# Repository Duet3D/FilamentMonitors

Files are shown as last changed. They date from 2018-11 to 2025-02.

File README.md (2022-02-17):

# Duet3D Filament monitor hardware source files:

2 Variations:

## Magnetic Filament Monitor

https://www.duet3d.com/magneticfilamentmonitor

Documentation:
https://docs.duet3d.com/Duet3D_hardware/Accessories/Rotating_Magnet_Filament_Monitor

## Laser Filament Monitor
_This is no longer produced_

Documentation for reference:
https://docs.duet3d.com/Duet3D_hardware/Accessories/Laser_Filament_Monitor

## Support requests

Please use the [forum](https://forum.duet3d.com) for support requests.

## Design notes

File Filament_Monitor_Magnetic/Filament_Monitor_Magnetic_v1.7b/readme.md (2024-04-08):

Note the PCB version 1.17b was renamed to version 3.0 so the entire MFM assembly (enclosure, hobbed magnet assembly and PCB) is named version 3.

The PCB itself is unchabed other than the sikscreen labelling.

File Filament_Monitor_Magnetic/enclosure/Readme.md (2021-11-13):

Note: The enclosure is not specifically designed for FDM printing - it is possible to print it on an FDM machine but layer height tweaking/sanding will be required to acheive the correct magnet to sensor offset.

If you have issues downloading the individual stls there is a zip containing all three.

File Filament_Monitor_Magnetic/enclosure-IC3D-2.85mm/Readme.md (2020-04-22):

This enclosure design was kindly provided by IC3D https://ic3dprinters.com/

They made the following changes:

* Thickened the overall body by 3mm
* Switched from using the plastic alignment ‘bumps’ to using 3mm stainless alignment pins
* Adjusted the position of the alignment pins
* Adjusted the filament through hole to 3mm dia.
* Printed in PCPBT

Please note it is still under development. Any questions please use the Duet3D forum: https://forum.duet3d.com/category/17/filament-monitor

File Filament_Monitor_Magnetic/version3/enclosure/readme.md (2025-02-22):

This is the FDM 3d printable version of the housing. Use this if you want to print your own housing.

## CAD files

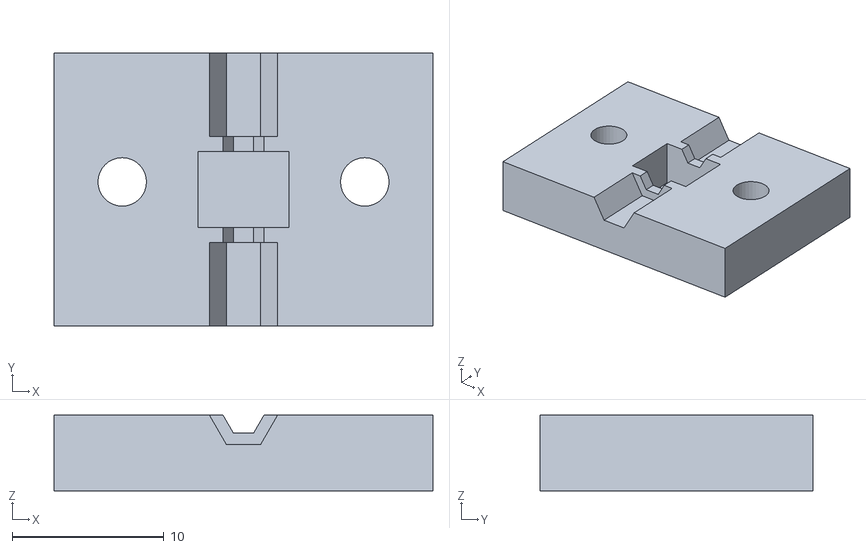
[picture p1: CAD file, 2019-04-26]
Filament_Monitor_Laser/Filament_Monitor_Laser_v2.0/LaserFilamentSensorHousing_DC42_new_lid.stl
25.0 x 18.0 x 5.00

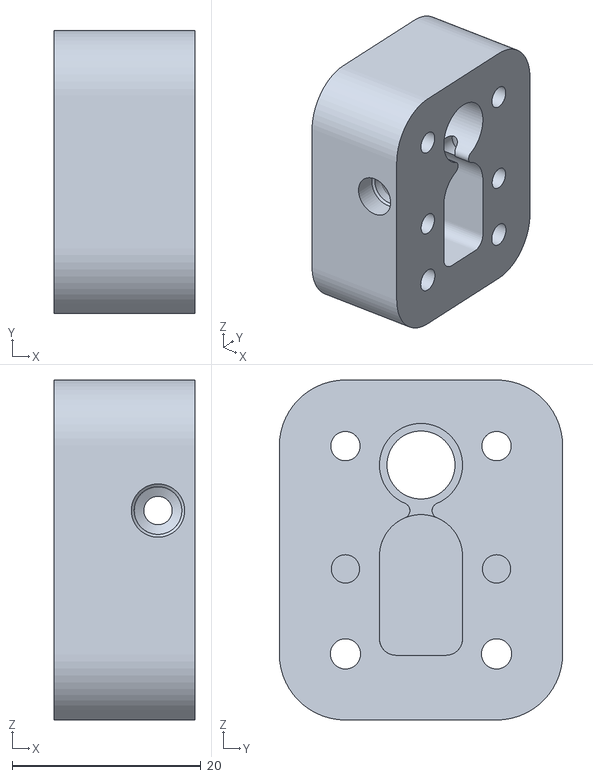
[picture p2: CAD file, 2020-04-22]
Filament_Monitor_Magnetic/enclosure-IC3D-2.85mm/Body.stl
14.9 x 30.0 x 36.0

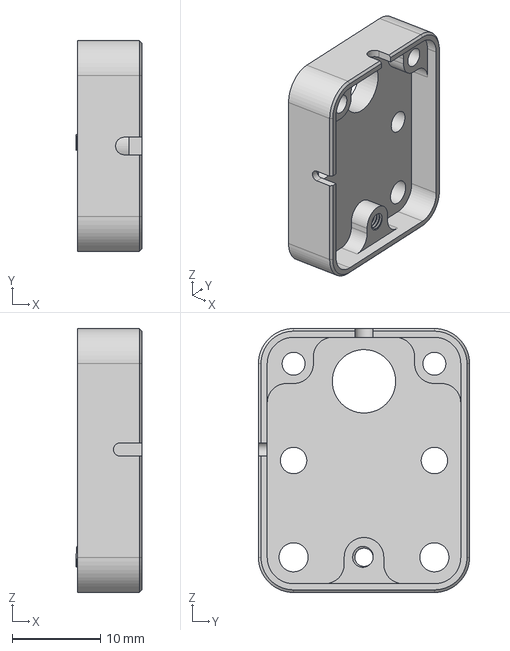
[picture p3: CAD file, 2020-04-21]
Filament_Monitor_Magnetic/enclosure/MFM_enc_lid.step
7.50 x 24.0 x 30.0 mm

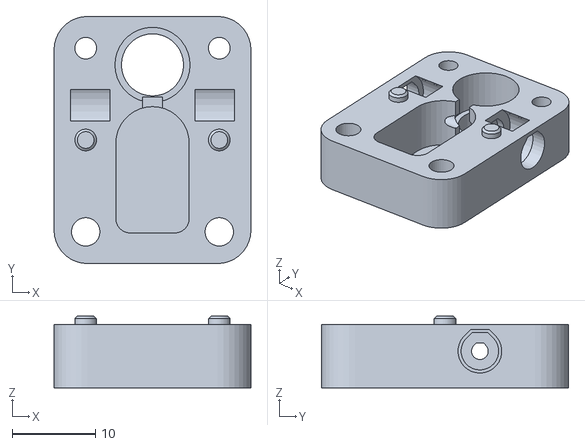
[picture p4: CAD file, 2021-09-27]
Filament_Monitor_Magnetic/enclosure_v2/MFM_Body_v2_m3_clearance_for_mounting.stl
23.6 x 29.6 x 8.60

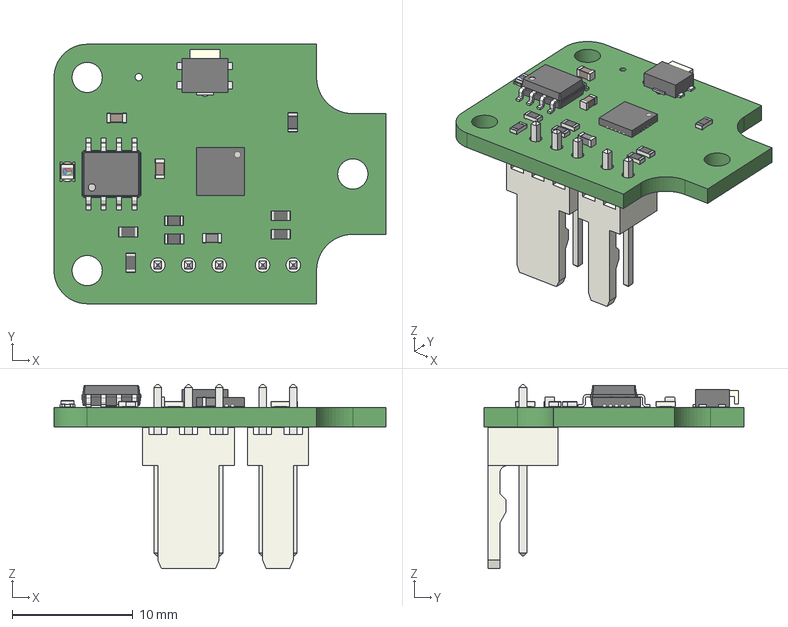
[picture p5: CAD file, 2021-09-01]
Filament_Monitor_Magnetic/Filament_Monitor_Magnetic_v1.7a/FilamentMonitor_v1.7a.step
27.5 x 21.5 x 15.3 mm

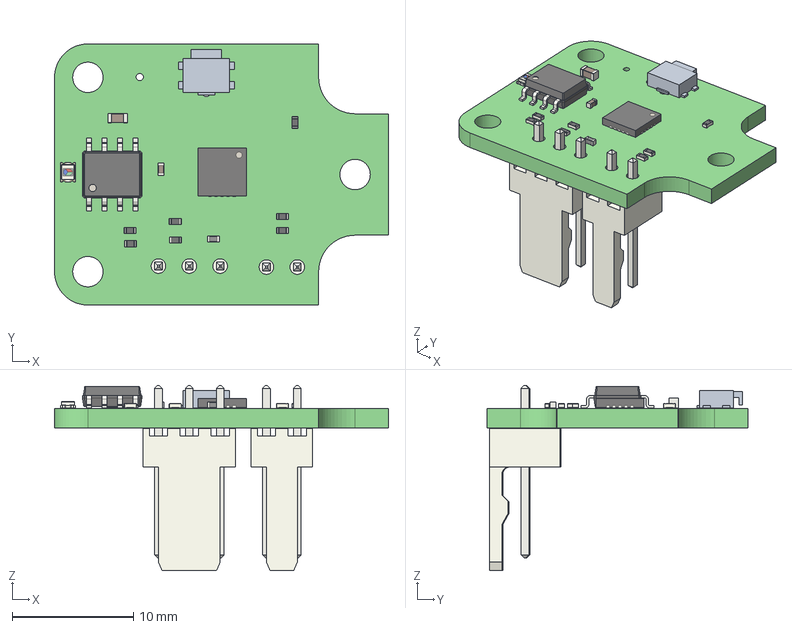
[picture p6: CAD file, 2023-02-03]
Filament_Monitor_Magnetic/Filament_Monitor_Magnetic_v1.7b/FilamentMonitor.step
27.5 x 21.5 x 15.3 mm
_autosave-FilamentMonitor PCB

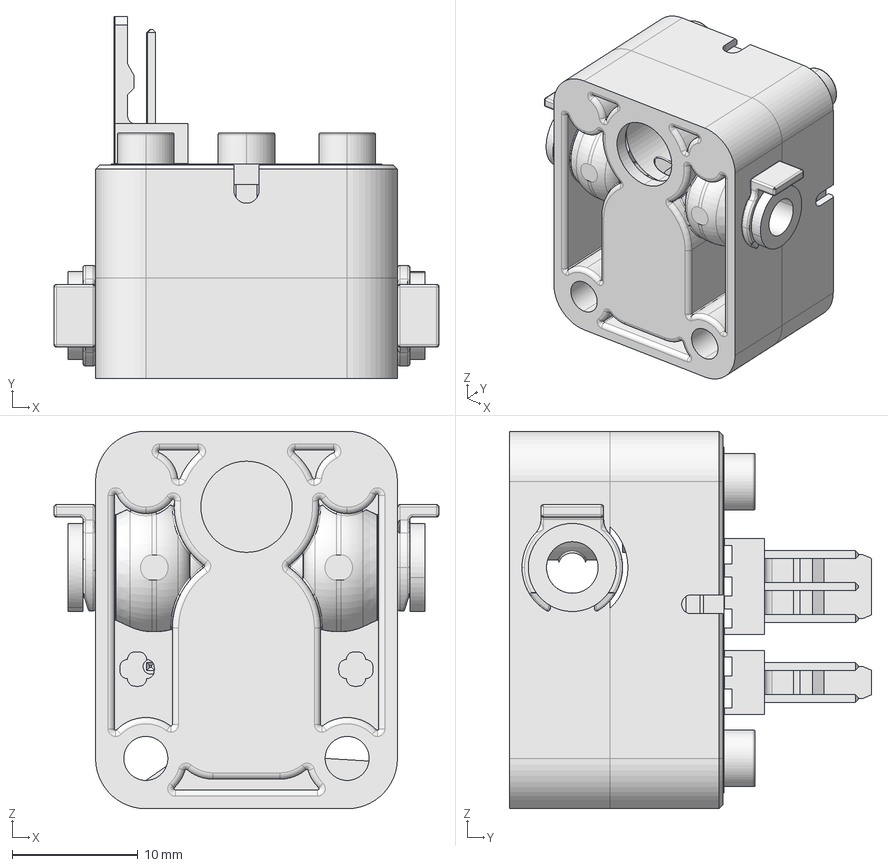
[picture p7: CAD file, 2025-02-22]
Filament_Monitor_Magnetic/version3/assembly/FILAMENT-MONITOR-v3.STEP
30.6 x 28.8 x 30.0 mm

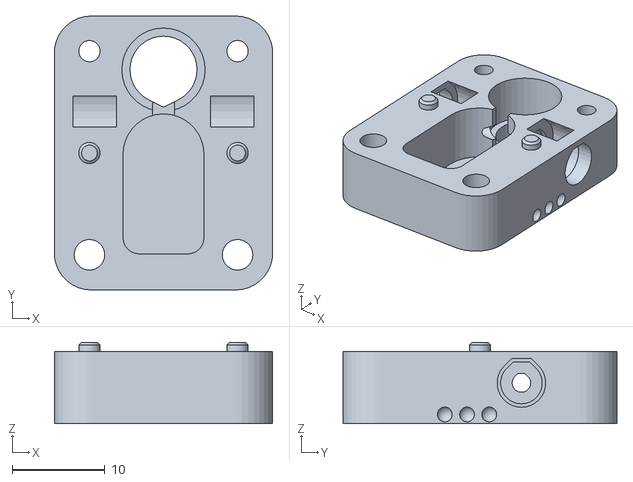
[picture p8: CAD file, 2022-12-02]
Filament_Monitor_Magnetic/version3/enclosure/MFM_enclosurev3_body_seam_0.2layer1_m3_clearance.stl
23.6 x 29.6 x 8.80

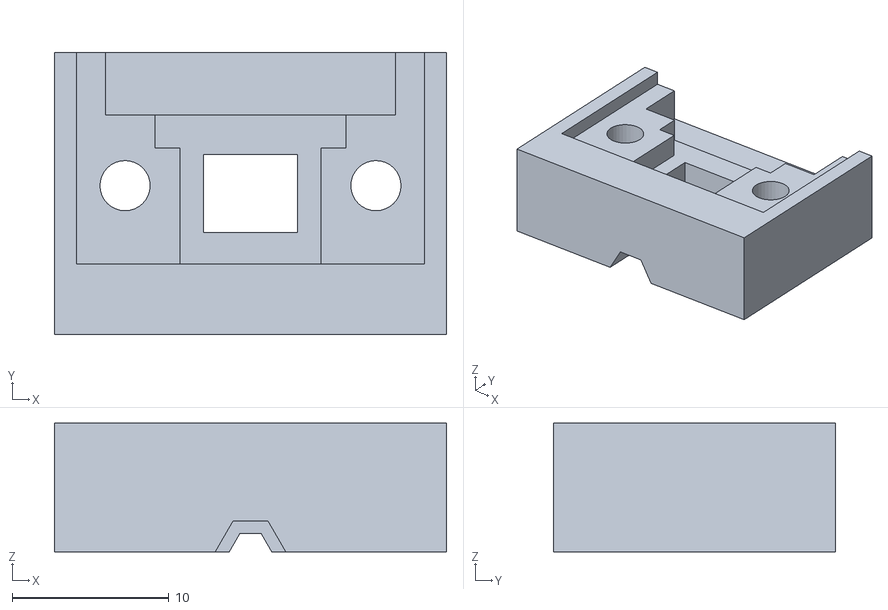
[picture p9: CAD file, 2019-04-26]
Filament_Monitor_Laser/Filament_Monitor_Laser_v2.0/LaserFilamentSensorHousing_DC42_new_base.stl
25.0 x 18.0 x 8.20

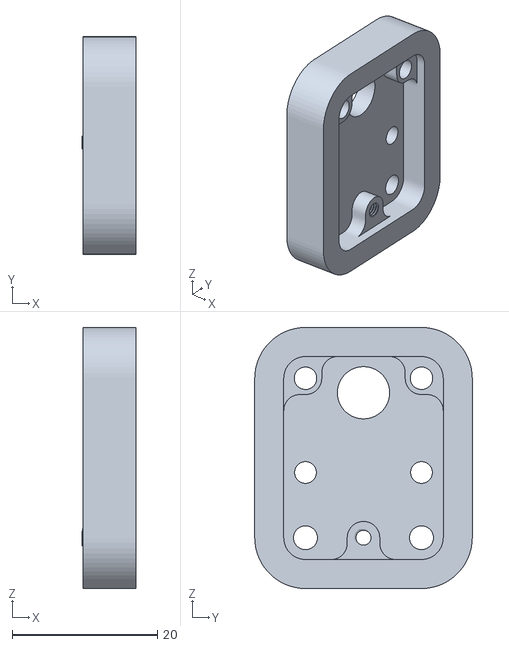
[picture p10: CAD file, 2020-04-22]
Filament_Monitor_Magnetic/enclosure-IC3D-2.85mm/lid.stl
7.50 x 30.0 x 36.0

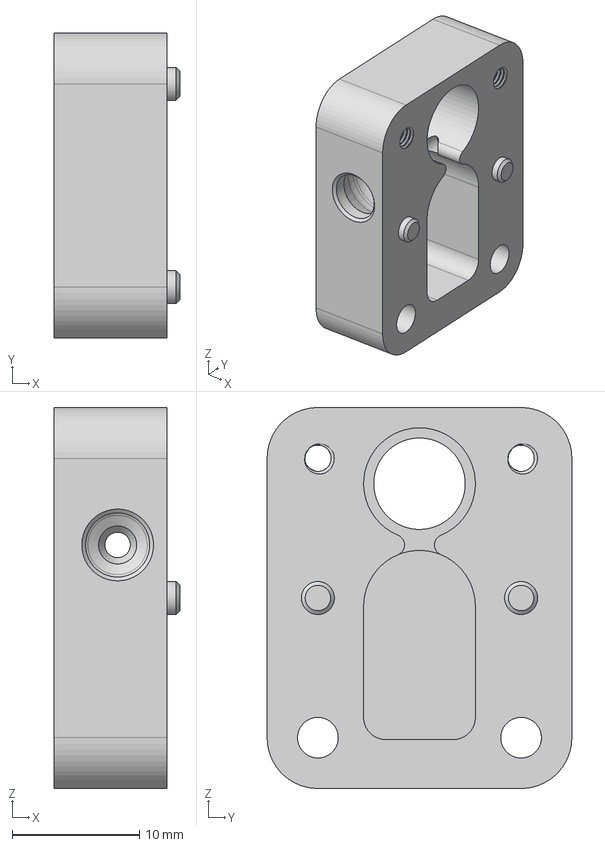
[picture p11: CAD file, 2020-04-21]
Filament_Monitor_Magnetic/enclosure/MFM_enc_body.step
9.90 x 24.0 x 30.0 mm

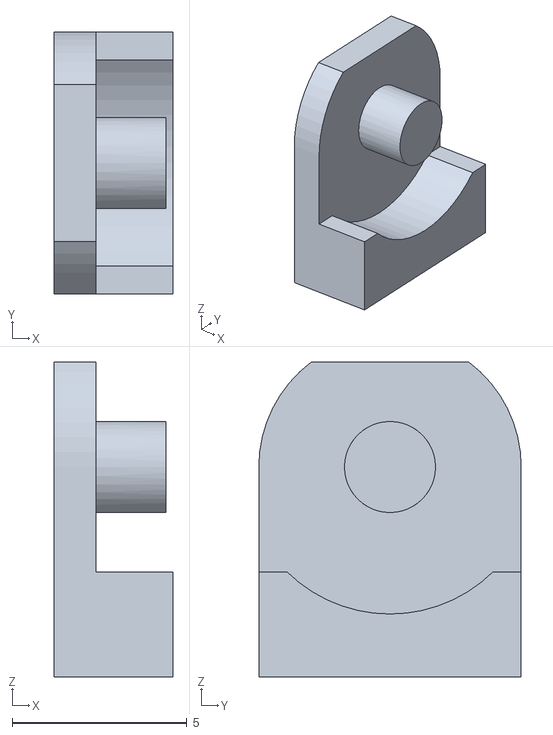
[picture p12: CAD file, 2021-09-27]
Filament_Monitor_Magnetic/enclosure_v2/MFM_Idler_v2_print2.stl
3.40 x 7.50 x 9.00

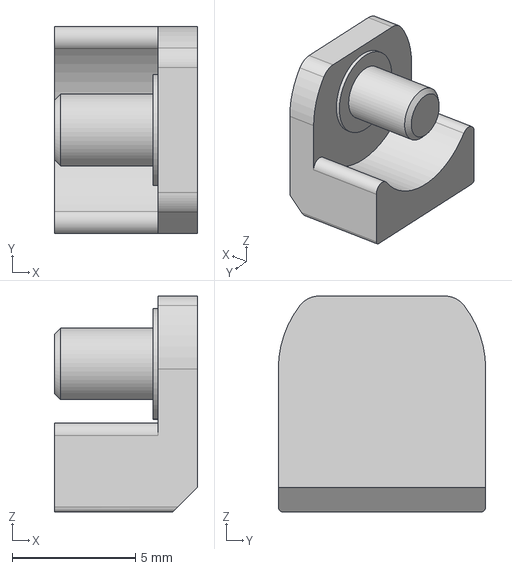
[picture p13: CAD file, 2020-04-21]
Filament_Monitor_Magnetic/enclosure/MFM_enc_idler.step
5.80 x 8.40 x 8.75 mm

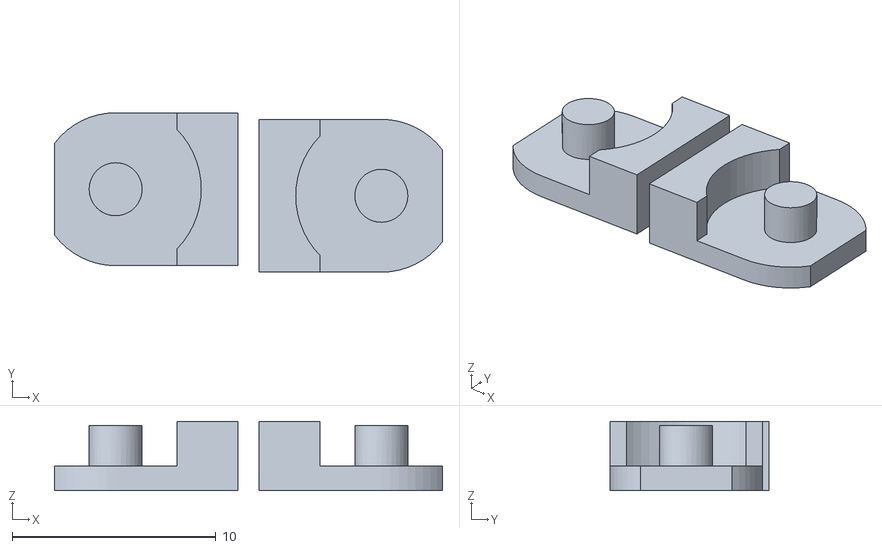
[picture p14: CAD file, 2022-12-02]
Filament_Monitor_Magnetic/version3/enclosure/MFM_Idler_v3_x2.stl
19.0 x 7.82 x 3.40

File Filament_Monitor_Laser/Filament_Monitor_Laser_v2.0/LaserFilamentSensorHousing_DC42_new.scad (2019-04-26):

/* [Hidden] */
// Duet3D laser filament sensor housing by D. Crocker, Escher 3D

/* [Options] */

// Select the PCB version of the filament monitor. Version 2 has the LED in the corner.
version = 2;						// [1,2]

// Select height of the filament centre above the PCB
filamentHeight=7;				// [4:0.2:9]

// Select the nominal diameter of the cutout for the PTFE tube. This needs to be somewhat larger than the outside diameter of the tube, but small enough to grip the tube when the two pieces are fastened together.
tubeDiameter=4.5;				// [4.0:0.1:5.2]

// Select the nominal diameter of the holes in the tube end stops for the filament to pass through. This needs to be somewhat larger than the outside diameter of the filament to prevent it rubbing, but smaller than the outside diameter of the tubing.
innerDiameter=2.7;				// [2.0:0.1:4.2]

// Do you want the top to be open or closed?
closedTop = 1;					// [0:Open,1:Closed]

/* [Hidden] */

width=25;
depth=(version == 1) ? 15 : 18;
holeSpacing=16;

boardWidth=22.2;					// added 0.2mm clearance
boardComponentsWidth1=18.5;
boardComponentsWidth2=9;
boardComponentsWidth3=12.2;
boardComponentsHeight1=2.8;		// the deepest parts are the connector spills
boardComponentsHeight2=2.0;		// the deepest parts are the connector spills

holeInsetDepth1=5;
holeInsetDepth2=4.5;
holeInsetDepth3=2.4;
boardDepth=9.5;
boardThickness=1.2;
stopThickness=1.0;

topHeight=4;
innerTubeDiameter=2.5;
chipDepth= (version == 1) ? 4 : 5;
chipOffset = (version == 1) ? 0 : -0.5;
chipWidth=6;
M3clear=3.2;
M3head=7.5;

overlap=0.2;

module cubeXY(x,y,z) {
	translate([-x/2, -y/2, 0]) cube([x,y,z]);
}

module cubeX(x,y,z) {
	translate([-x/2, 0, 0]) cube([x,y,z]);
}

module FilamentGroove() {
	translate([0, -depth/2-overlap, 0]) rotate([-90,0,0]) cylinder(r=innerDiameter/2,h=99,$fn=6);
	translate([0, chipDepth/2+chipOffset+stopThickness, 0]) rotate([-90,0,0]) cylinder(r=tubeDiameter/2,h=99,$fn=6);
	translate([0, -chipDepth/2+chipOffset-stopThickness, 0]) rotate([90,0,0]) cylinder(r=tubeDiameter/2,h=99,$fn=6);
}

module Base(thickness) {
	difference() {
		translate([0,chipOffset,0]) cubeXY(width,depth,thickness+boardThickness);
		translate([-holeSpacing/2,0,-overlap]) cylinder(r=M3clear/2, h=99, $fn=32);
		translate([holeSpacing/2,0,-overlap]) cylinder(r=M3clear/2, h=99, $fn=32);
		FilamentGroove();
		translate([0,chipOffset,-overlap]) cubeXY(chipWidth, chipDepth, thickness+2*overlap);
		translate([0,-holeInsetDepth1, thickness]) cubeX(boardWidth,depth, boardThickness+overlap);
		translate([0,+holeInsetDepth2, thickness-boardComponentsHeight1])
			cubeX(boardComponentsWidth1, depth, boardComponentsHeight1+overlap);
		translate([0,-holeInsetDepth1, thickness-boardComponentsHeight2])
			cubeX(boardComponentsWidth2, depth, boardComponentsHeight2+overlap);
		if (version == 1) {
			// Cutout for LED
			translate([-20,holeInsetDepth2,thickness-boardComponentsHeight2]) cube([20,5,10]);
		}
		if (version == 2) {
			// Version 2 prototype has additional SMD components that we need to clear
			translate([0,+holeInsetDepth3, thickness-boardComponentsHeight2])
				cubeX(boardComponentsWidth3, depth, boardComponentsHeight2+overlap);
		}
	}
}

module Top(thickness, isClosed) {
	difference() {
		translate([0,chipOffset,0]) cubeXY(width,depth,(isClosed) ? thickness + 1 : thickness);
		translate([0,chipOffset,(isClosed) ? 1 : -overlap]) cubeXY(chipWidth, chipDepth, thickness+2*overlap);
		translate([-holeSpacing/2,0,-overlap]) cylinder(r=M3clear/2, h=99, $fn=32);
		translate([holeSpacing/2,0,-overlap]) cylinder(r=M3clear/2, h=99, $fn=32);
		translate([0,0,(isClosed) ? thickness + 1 : thickness]) FilamentGroove();
	}
}

Base(filamentHeight);
//translate([0, 25, 0]) Top(topHeight, closedTop);

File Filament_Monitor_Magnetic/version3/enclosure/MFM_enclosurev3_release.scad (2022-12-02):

//what to build
build = "both"; // "lid", "body" or "both"

//parametric adjustments
740ZZ_adjustment_r=0.12; // (was 0.22 previously)//added to 7mm bearing radius to ensure bearing can fit in the hole but is held securely with no XY slop
M2_5_r=2.3/2; //screw directly into the plastic, adjust based on how slicer deals with small holes (Ideamaker = 2.6/2 S3D = 2.4/2 , superslicer 2.3
M3_r=2.9/2; //screw directly into the plastic, adjust based on how slicer deals with small holes
peg_adjustment_r=0.3;// clearance between the peg and the peg hole, adjust depending on how the slicer deals with small holes. (ideamaker = 0.3, S3D= 0.4)
lid_t_adjust=0.8; //adjust to get a good agc (<100) without the magnet scraping too hard on the sensor. needs to bein multiples of the layerheigh but can adjust first layer  add 0.1
body_t_adj=0.1; //amount to add to the body height to make it print in nice layers (does not impact the magnet offset as added to the bottom of the body)
body_bearing_adj=-0.4; //amount to push the body bearing down into the body so that the magnet assembly is clamped in Z with no play in Z. Note for this should be a multiple of the layer height used. 0.2 = default
mounting=0; //If mounting is set to 1 then the M3 holes in the body will be clearance holes to allow M3 bolts to pass through the whole assembly so it can be mounted on a plate or similar. If Mounting is set to 0 the M3 holes in the body will be undersized for an M3 screw to tap into.
idler_w_adjust=-0.05; //some slicers make the idler channel t0o wide and the idler slops around.
filament_path_adjust=0.35;// how much to push the filament path up against the hobbed part
print_seam_radius=0.4; //amount to add on vertical cylinders as a small cut out to hide the print seam in.


//component dimensions
shape_rr_r=4;
740ZZ_or=7/2+740ZZ_adjustment_r;
740ZZ_t=2.5;
740ZZ_f_t=0.8; //0.6 specified. 0.8 with interference from printed part surface.
MFM_assy_or=8/2;
MFM_assy_clearance_or=MFM_assy_or+0.5;
MFM_assy_l=12.2;
MFM_assy_bearing_l=2.3;
MFM_assy_knurl_l=4.0+0.2+0.2;// was 3.8+0.2+0.2 in prototypes 
idler_w = 8.8+idler_w_adjust;
idler_h = 6.9;
idler_rect_l = 10.75;
idler_cyl_off=-9.5+filament_path_adjust;
idler_rr_r=3.5/2;
collet_bore_r= 7.2/2;
collet_neck_t=2;
collet_bore_l= 6.7-collet_neck_t;
collet_r=5.25/2;
PTFE_or=4.5/2; //needs to be oversized to be printable
PTFE_inset_l=0.6; //shortend to 0.6 as gaps occured on PS
peg_r=2.6/2-peg_adjustment_r/2; //half the adjustment to shrink the peg
peg_t=1;
M2_5_clearance_r=3.2/2;
M3_cords=[[-8,-20],[8,-20]];
M3_clearance_r=3.3/2;
peg_cords=[[-8,-9],[8,-9]];
peg_clearance_r=peg_r+peg_adjustment_r/2; //half the adjustment to grow the hole.
PCB_enc_wall_t=0.8;
PCB_t=1.5;
PCB_w=22;
PCB_l=28;
PCB_comp_h=2.7;
PCB_soff_r=5.5/2;
PCB_standoff_fillet_r=(3.4+PCB_enc_wall_t)/2;
PCB_offset_x=0;
PCB_offset_y=-PCB_l/2+5;
PCB_mount=[[-8,2],[0,-20],[8,2]];
PCB_mount_clearance=0.25;
slot_r=2/2;
slot_off=[[-11,-7.75,1.7],[0,5,1.7]];
cut_adjst=0.1;
lid_t=3.8+lid_t_adjust;
body_t=740ZZ_t+MFM_assy_knurl_l+740ZZ_f_t+body_t_adj;
filament_inlet_r=3/2;
filament_clearance_r=2/2;
filament_r=1.75/2; //other adjustments required to the model other than just changing this to make it work with 2.85mm filament
filament_cut_w=2.4;
filament_path=[0,-MFM_assy_or-filament_r+filament_path_adjust,740ZZ_t+filament_clearance_r+740ZZ_f_t+body_t_adj];
//echo (abs(body_bearing_adj));
$fn=36;
v3_mark_r=0.8;
v3_mark_off=[11.8,-8,v3_mark_r+0.2];

//select part to generate
if (build == "lid")
    lid();
else if (build == "body")
    body();
else if (build == "both"){
    lid();
    translate([0,15,0])
        rotate([0,0,180])
            body();
}


module body(){
    difference(){
        union(){
            translate([PCB_offset_x,PCB_offset_y,0])
                roundedRect([PCB_w+PCB_enc_wall_t*2,PCB_l+PCB_enc_wall_t*2,body_t],shape_rr_r,$fn=36);
            for(i=[0,1])
                translate([peg_cords[i][0],peg_cords[i][1],body_t+peg_t/2])
                    hull(){
                        translate([0,0,-0.2])
                            cylinder(h=peg_t-0.2,r=peg_r,center=true, $fn=36);
                        cylinder(h=peg_t,r=peg_r-0.3,center=true, $fn=36);
                    }
        }
        //holes
        for(i=[0,2])
            translate([PCB_mount[i][0],PCB_mount[i][1],body_t/2]){
                cylinder(h=body_t+1,r=M2_5_r,center=true, $fn=36);
            }
        for(i=[0,1]){
            translate([M3_cords[i][0],M3_cords[i][1],body_t/2])
                if (mounting)
                    cylinder(h=body_t+1,r=M3_clearance_r,center=true, $fn=36);
                else
                    cylinder(h=body_t+1,r=M3_r,center=true, $fn=36);
            }
       translate([0,0,(body_t+740ZZ_t+cut_adjst)/2+body_t_adj+body_bearing_adj/2])
            cylinder(h=body_t-740ZZ_t+cut_adjst+abs(body_bearing_adj),r=MFM_assy_clearance_or,center=true, $fn=36);   
        translate([0,0,(body_t-cut_adjst)/2])
         seamCylinder(height=body_t+cut_adjst,radius=740ZZ_or,seamr=print_seam_radius,c=true, faces=36);   
        //idler
        translate([0,idler_cyl_off,body_t-idler_h/2+cut_adjst/2])
            cylinder(h=idler_h+cut_adjst,r=idler_w/2,center=true, $fn=36);
        translate([0,idler_cyl_off-(idler_rect_l-idler_rr_r)/2,body_t-idler_h])
            roundedRect([idler_w,idler_rect_l+idler_rr_r,idler_h+cut_adjst],idler_rr_r,$fn=24);
        translate([0,filament_path[1],(body_t+740ZZ_t+cut_adjst)/2+body_bearing_adj/2])
            cube([filament_cut_w,filament_clearance_r*2,body_t-740ZZ_t+cut_adjst+abs(body_bearing_adj)],center=true);
        //filament path
        translate([filament_path[0],filament_path[1],filament_path[2]]){
            teardrop(filament_clearance_r, PCB_w+PCB_enc_wall_t*2+cut_adjst,true);
            for(i=[-1,1]){
                translate([i*((PCB_w+PCB_enc_wall_t*2-collet_neck_t)/2),0,0])
                    teardrop(collet_r, collet_neck_t+2,true);
                translate([i*((PCB_w+PCB_enc_wall_t*2-collet_bore_l)/2-collet_neck_t),0,0])
                    teardrop(collet_bore_r, collet_bore_l,true);
                translate([i*((PCB_w+PCB_enc_wall_t*2-PTFE_inset_l)/2-collet_bore_l-collet_neck_t),0,0])
                    teardrop(PTFE_or, PTFE_inset_l+cut_adjst,true);                   
                
           }
        }
     //V3 markings
            for(i=[0,1,2]){
             translate([v3_mark_off[0],v3_mark_off[1]-v3_mark_r*3*i,v3_mark_off[2]])
                sphere(r=v3_mark_r);
            }           
    }
}
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

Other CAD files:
Filament_Monitor_Magnetic/version3/enclosure/MFM_enclosurev3_body_seam_0.2layer1.stl
Filament_Monitor_Magnetic/enclosure_v2/MFM_Body_v2.stl
Filament_Monitor_Magnetic/enclosure_v2/MFM_Lid_v2.stl
Filament_Monitor_Magnetic/version3/enclosure/MFM_enclosurev3_lid_seam_0.2layer1.stl
Filament_Monitor_Laser/Filament_Monitor_Laser_v1.7/FilamentMonitor.step
Filament_Monitor_Magnetic/enclosure/MFM_enc_body.stl
Filament_Monitor_Magnetic/enclosure/MFM_enc_idler.stl
Filament_Monitor_Magnetic/enclosure/MFM_enc_lid.stl

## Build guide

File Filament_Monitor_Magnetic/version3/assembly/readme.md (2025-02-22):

This contains the assembled version of the V3 MFM as a step file to allow fit testing with custom printers/hotends etc.

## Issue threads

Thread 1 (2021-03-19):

Schematic / Layout for Filament Sensor v2

piflixe, 2021-03-19:
Hi there! I can't find the schematic or layout files anywhere for the v2 of the laser filament sensor.

Could someone please post the link the design files or push them here? kiCAD files would be sufficient, I can take care of PDF exports and the like.

Thank you so much!

T3P3, 2021-03-19:
https://github.com/Duet3D/FilamentMonitors/blob/master/Filament_Monitor_Laser_v2.0/LaserFilamentMonitor_Schematic_v2.0.pdf

HTH

Tony

piflixe, 2021-03-21:
Dear Tony @T3P3 ,
thank you so much for your quick reply! This is really helpful for me. I am trying to use the sensor and the whole sensor board for a different application, which looks really promising. Would you mind sharing the native design files (looks like kiCAD?) as well? I might need a board with more pins and a bigger processor so your design could be a good starting point. The plan is to release the results openSource as well so you might also benefit from it. If you do not want to push the files on github but would like to share them with me, please email to piela@konstruktiv-berlin.de
Thanks you!

piflixe, 2021-03-21:
I hope I do not bother you with these questions, just keen to know and hoping to be able to free some pins on the sensor boards
- is the LDP pin on the ATtiny actually switched or just used as a power supply?
- did you include the voltage regulator so the whole board becomes 5V resistant? Or should it still be used with 3,3V only?

T3P3, 2021-03-21:
They are in the latest commit (https://github.com/Duet3D/FilamentMonitors/commit/65b57c8e6b1f42bf2a952dd01901a3e57512fbc8).

Please so link to your new design files when its done 👍

piflixe, 2021-03-21:
Thank you so much for the quick reaction @T3P3 !

This is our git repository: https://gitlab.com/konstruktiv_berlin/laser-motion-sensor

There is nothing working there yet, still work in progress. Only the LEDs are blinking and I added interrupt functionality for the v1.7 board to read STP/DIR pins. But hopefully it will be functional soon.

Closed 2021-03-21.

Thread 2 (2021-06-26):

STL Files Corrupt

gamefanatic53, 2021-06-26:
LaserFilamentSensorHousing_DC42_new_base.stl
LaserFilamentSensorHousing_DC42_new_lid.stl
I will add the LaserFilamentMonitor_Schematic_v2.0.pdf won't open either.

These will no load into a slicer, or other application.  All state they are invalid.

chrishamm, 2022-01-22:
It is properly displayed in the GitHub STL viewer so I am closing this issue.

Closed 2022-01-22.

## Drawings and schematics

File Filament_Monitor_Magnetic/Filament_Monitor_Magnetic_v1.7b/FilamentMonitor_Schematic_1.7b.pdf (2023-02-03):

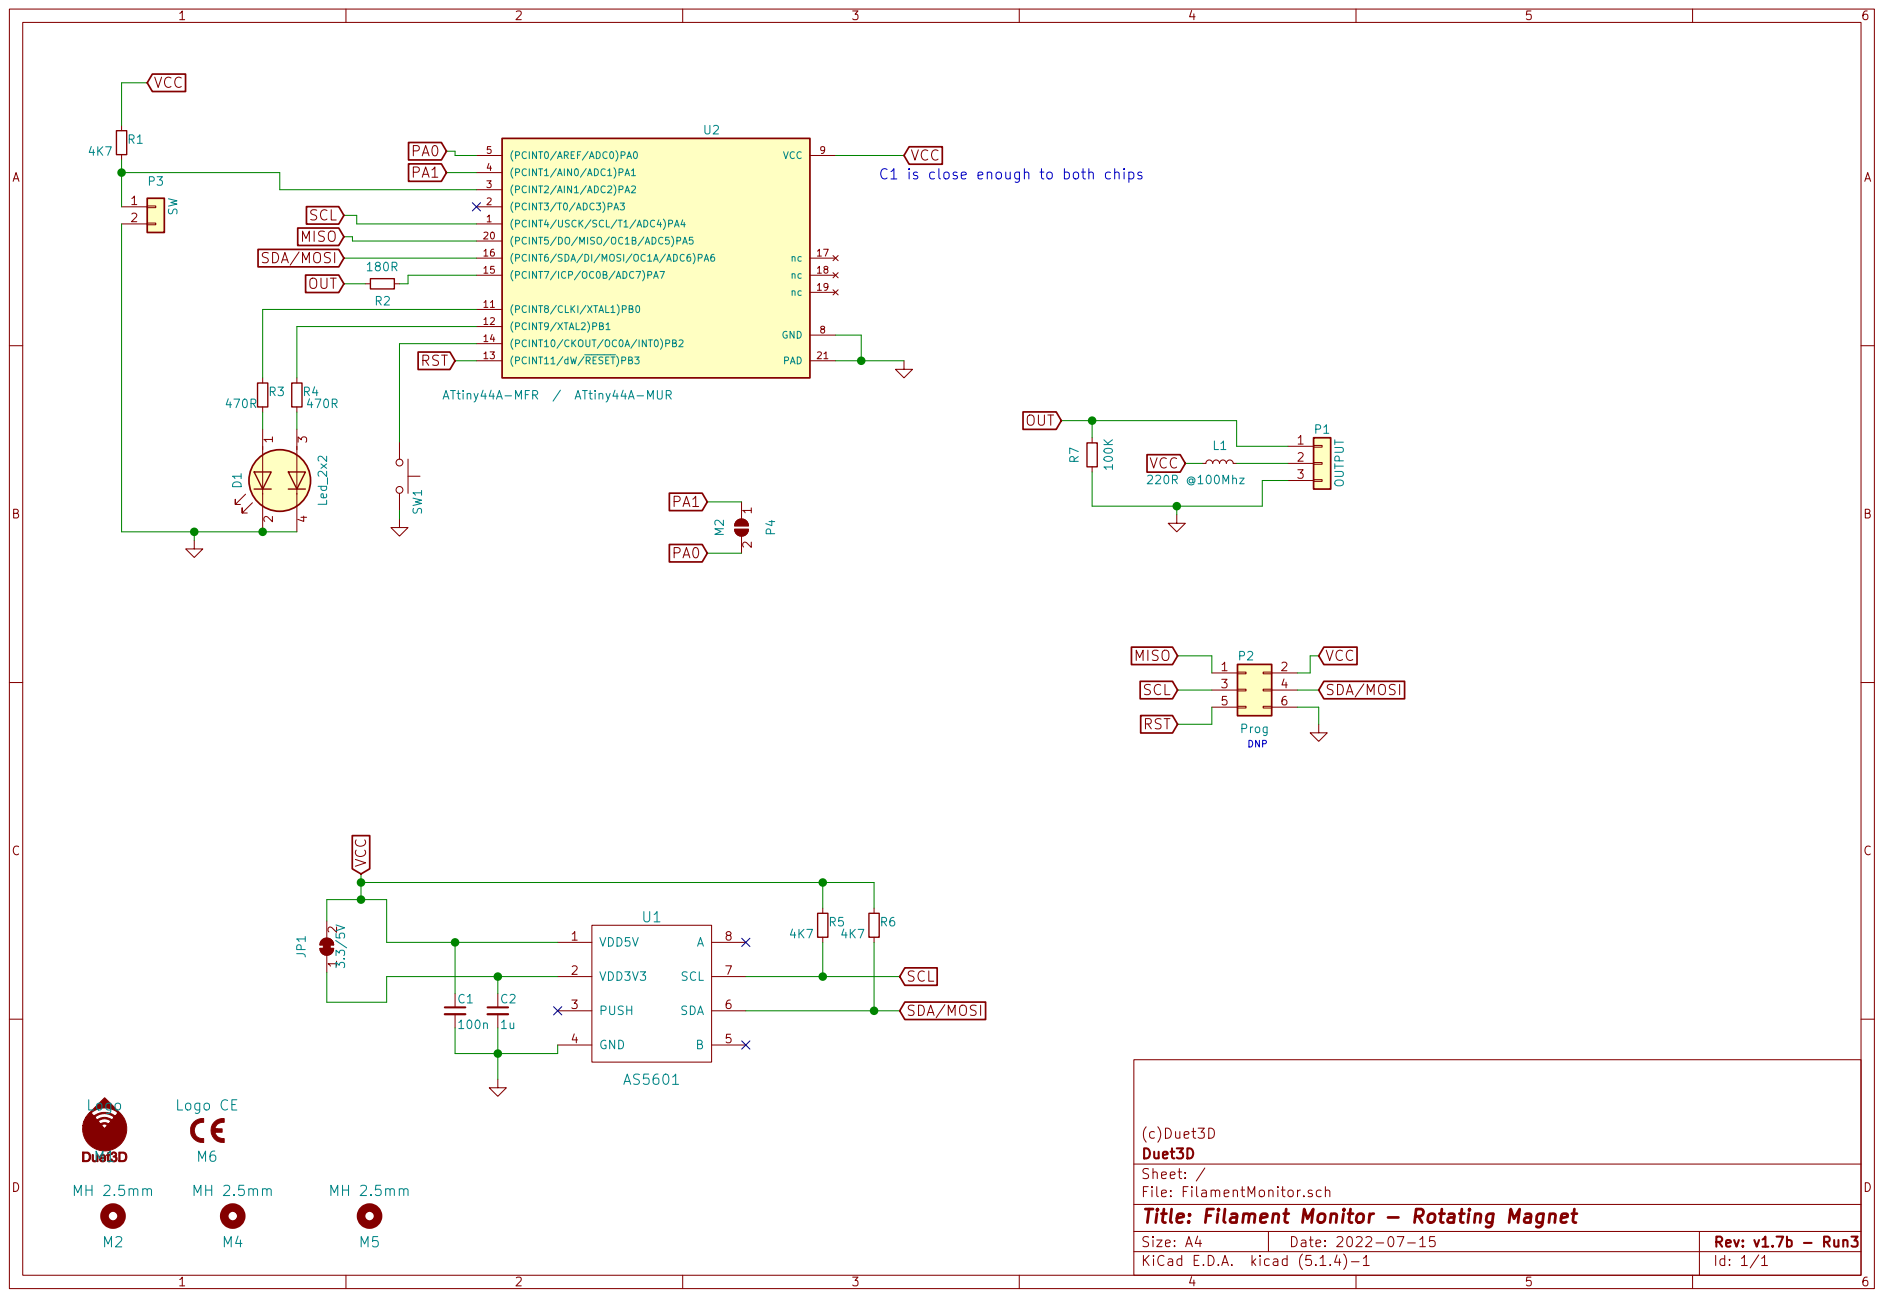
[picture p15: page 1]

VCC
DNP C1 is close enough to both chips

(c)Duet3D
Id: 1/1 Title: Filament Monitor - Rotating Magnet File: FilamentMonitor.sch Sheet: / Duet3D

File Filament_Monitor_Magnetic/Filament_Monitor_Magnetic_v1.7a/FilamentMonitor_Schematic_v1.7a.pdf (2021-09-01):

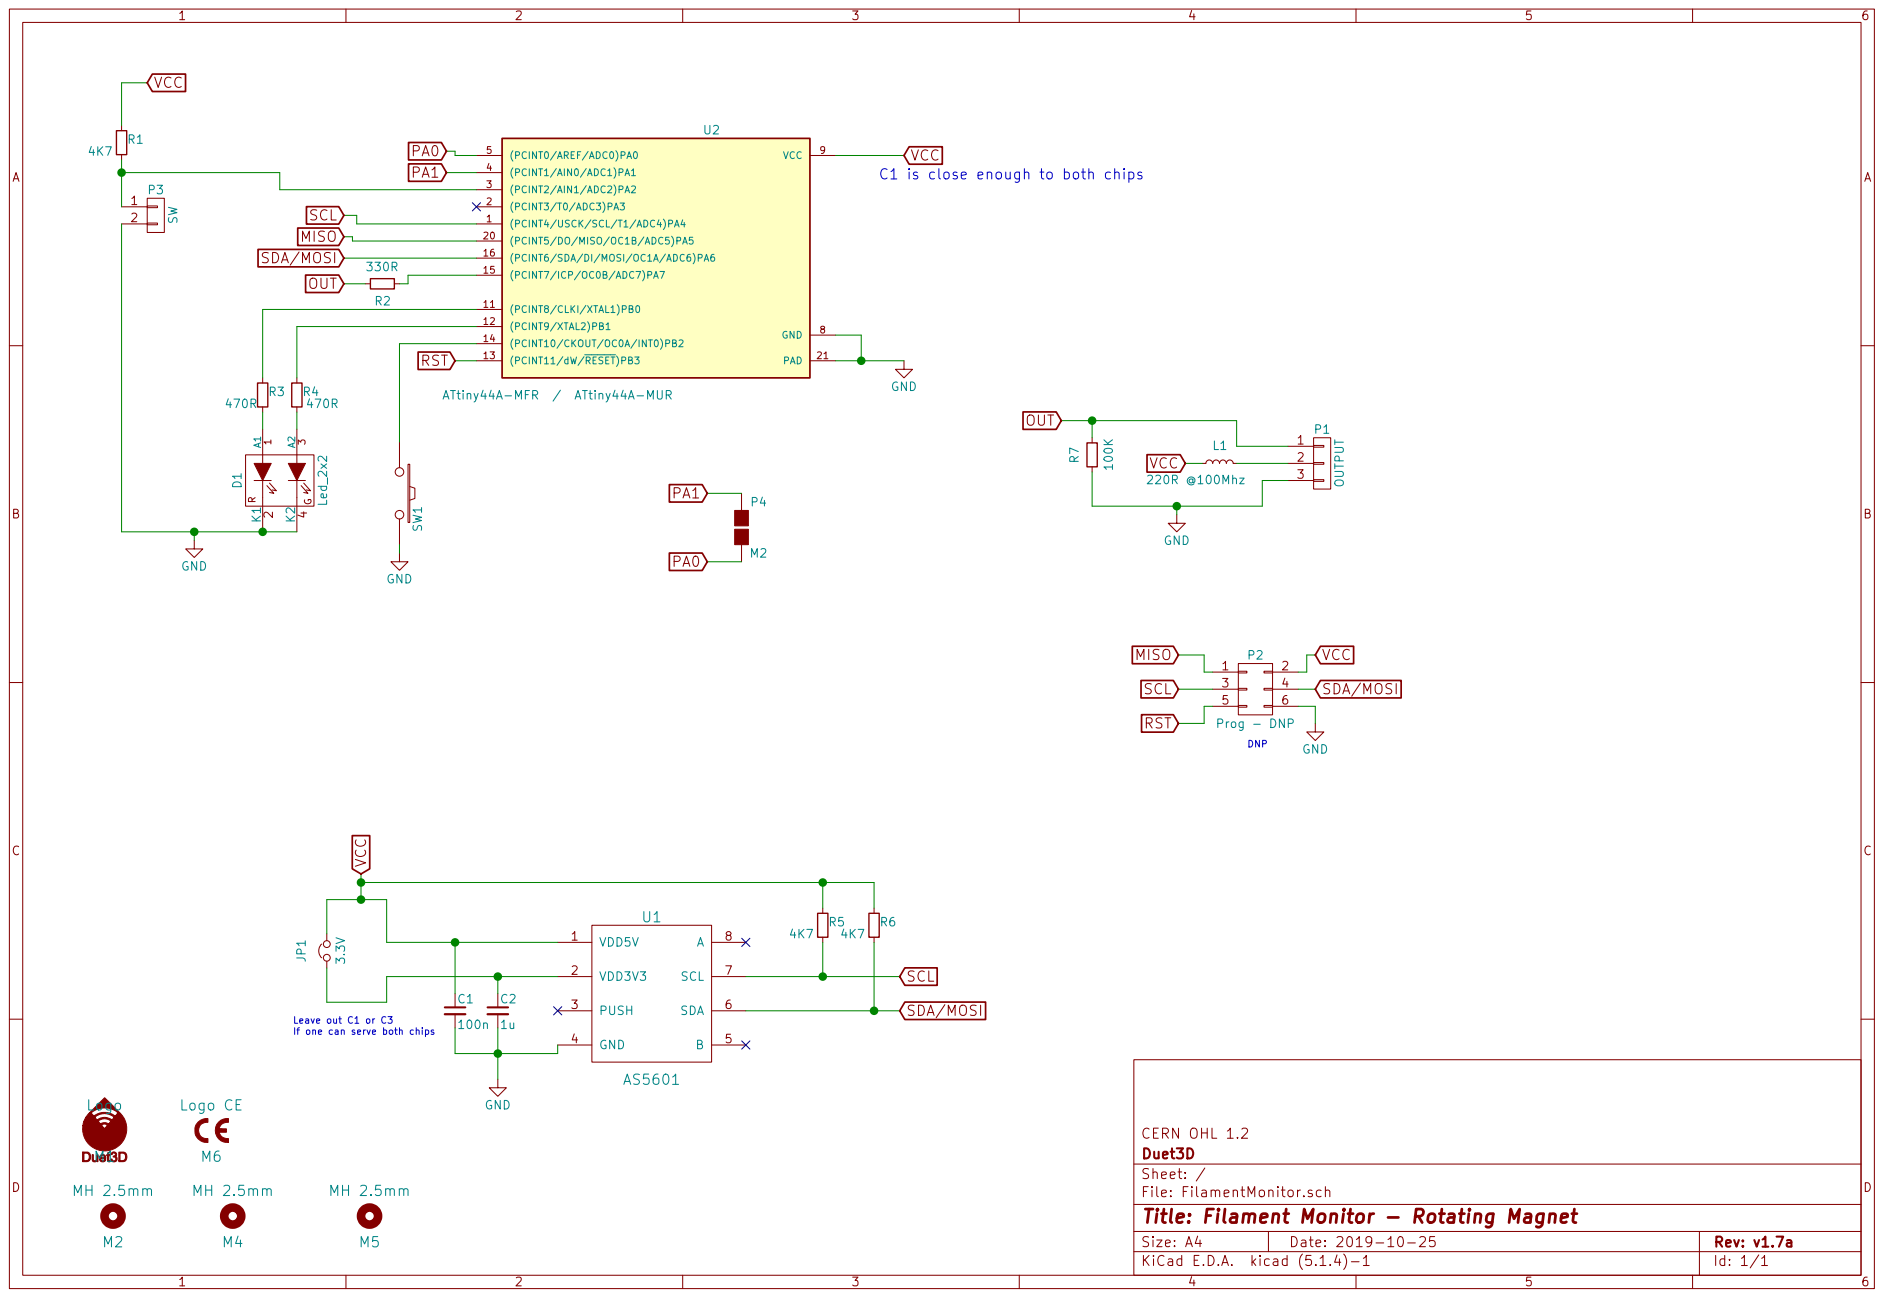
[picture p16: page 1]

VCC
C1 is close enough to both chips

Leave out C1 or C3
If one can serve both chips

Id: 1/1 Title: Filament Monitor - Rotating Magnet File: FilamentMonitor.sch Sheet: / Duet3D

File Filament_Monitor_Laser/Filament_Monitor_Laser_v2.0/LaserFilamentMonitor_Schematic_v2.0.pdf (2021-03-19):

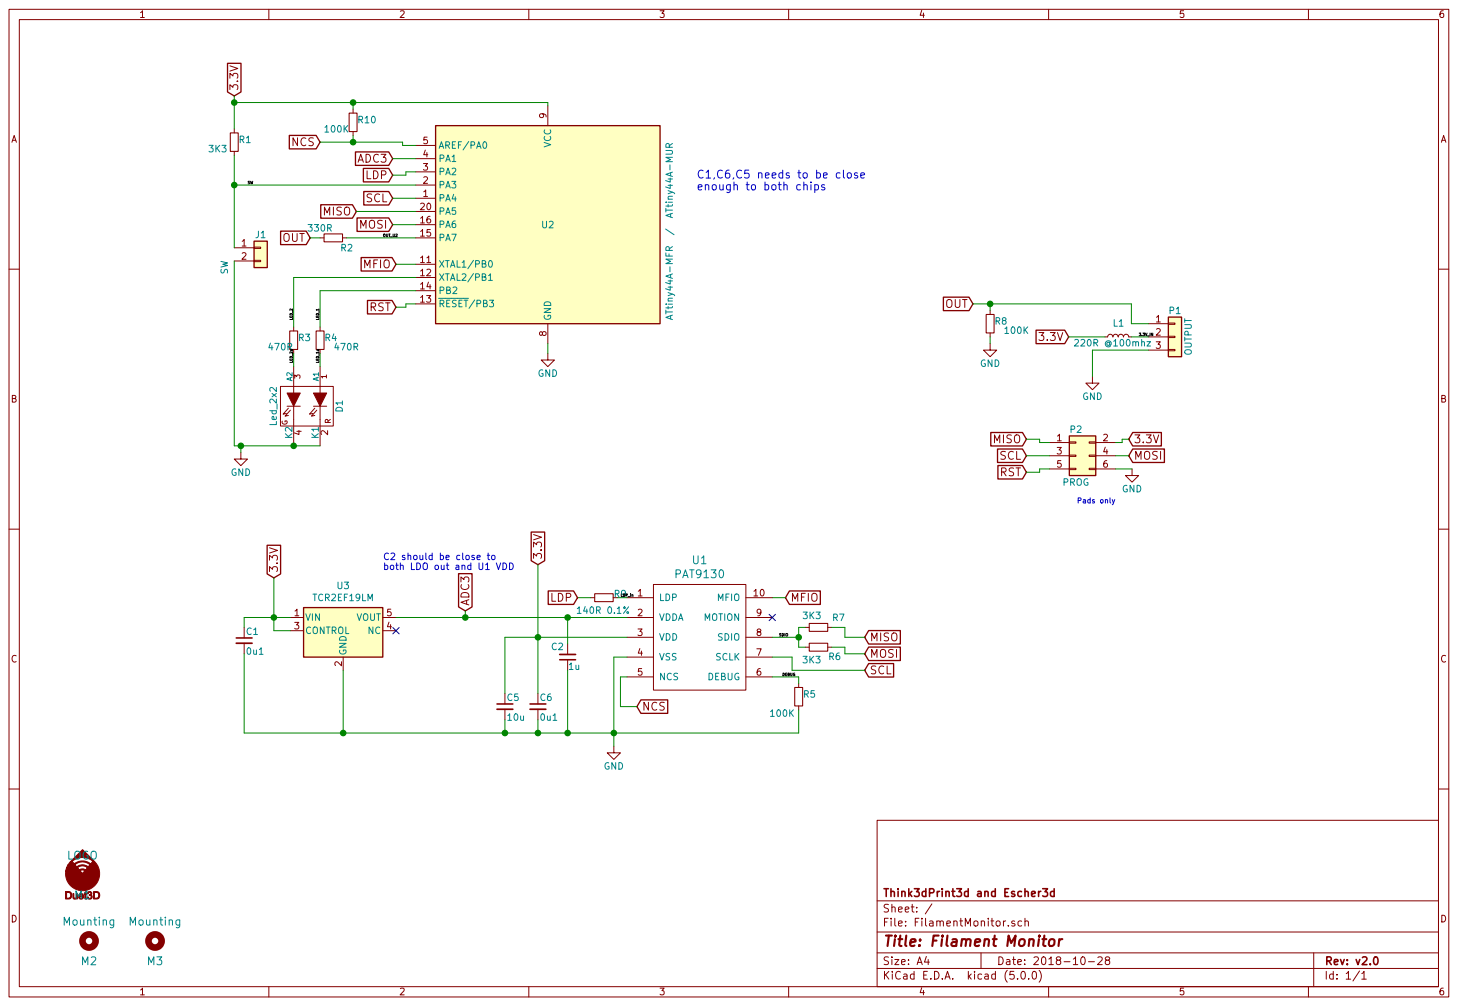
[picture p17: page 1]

enough to both chips 3.3V

Pads only C1,C6,C5 needs to be close

Id: 1/1 Title: Filament Monitor File: FilamentMonitor.sch Sheet: / Think3dPrint3d and Escher3d

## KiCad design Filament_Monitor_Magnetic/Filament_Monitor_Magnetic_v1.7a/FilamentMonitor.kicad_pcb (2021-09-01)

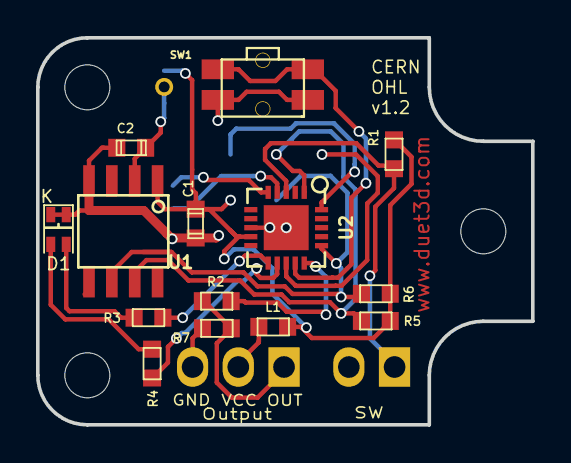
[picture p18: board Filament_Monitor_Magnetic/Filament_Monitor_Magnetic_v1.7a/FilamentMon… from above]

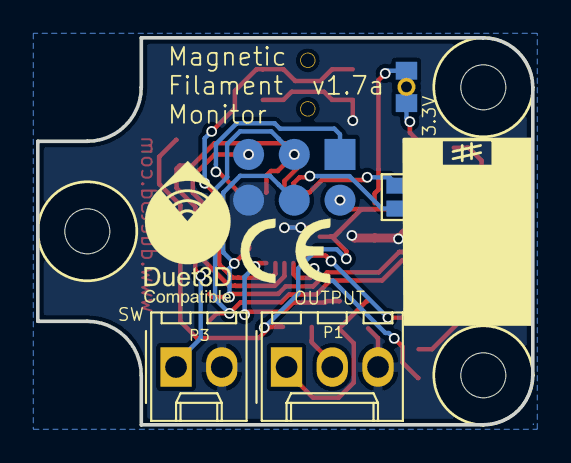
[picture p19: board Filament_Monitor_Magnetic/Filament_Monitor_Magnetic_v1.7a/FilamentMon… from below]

Board: 2 copper layers, 27.5 x 21.5 mm, 24 parts (10 on the bottom side), 18 nets.

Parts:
C1: 100n; C_0603
C2: 1u; C_0603
D1: Led_2x2; 2x2_SMD_LED_1.6x1.25mm
JP1: 3.3V; SJ_Bridged
L1: 220R @100Mhz; R_0603
M1: Logo; LOGO_Duet3dCompatible_xs
M2, M4, M5: MH 2.5mm; Fixing_M2.5_clearance_5.5
M6: Logo CE; Logo_CE_Tiny_mirror
P1: OUTPUT; Molex_KK-254_AE-6410-03A_1x03_P2.54mm_Vertical
P2: Prog - DNP; Test_Point_2x3
P3: SW; Molex_KK-254_AE-6410-02A_1x02_P2.54mm_Vertical
P4: M2; SJ
R1, R5, R6: 4K7; R_0603
R2: 330R; R_0603
R3, R4: 470R; R_0603
R7: 100K; R_0603
SW1: Push; SW_SIDE_1_lugs
U1: AS5601; SOIC-8
U2: ATtiny44A-MFR / ATtiny44A-MUR; QFN-20-1EP_4x4mm_P0.5mm_EP2.5x2.5mm

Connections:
GND: C1.2, C2.2, D1.2, D1.4, P1.3, P2.6, P3.2, R7.1, SW1.2, U1.4, U2.8, U2.21
MISO: P2.1, U2.20
unnamed: C2.1, JP1.1, U1.2
unnamed: D1.1, R3.2
unnamed: D1.3, R4.2
unnamed: L1.2, P1.2
unnamed: P3.1, R1.2, U2.3
unnamed: R2.1, U2.15
unnamed: R3.1, U2.11
unnamed: R4.1, U2.12
unnamed: SW1.1, U2.14
OUT: P1.1, R2.2, R7.2
PA0: P4.2, U2.5
PA1: P4.1, U2.4
RST: P2.5, U2.13
SCL: P2.3, R5.2, U1.7, U2.1
SDA/MOSI: P2.4, R6.2, U1.6, U2.16
VCC: C1.1, JP1.2, L1.1, P2.2, R1.1, R5.1, R6.1, U1.1, U2.9

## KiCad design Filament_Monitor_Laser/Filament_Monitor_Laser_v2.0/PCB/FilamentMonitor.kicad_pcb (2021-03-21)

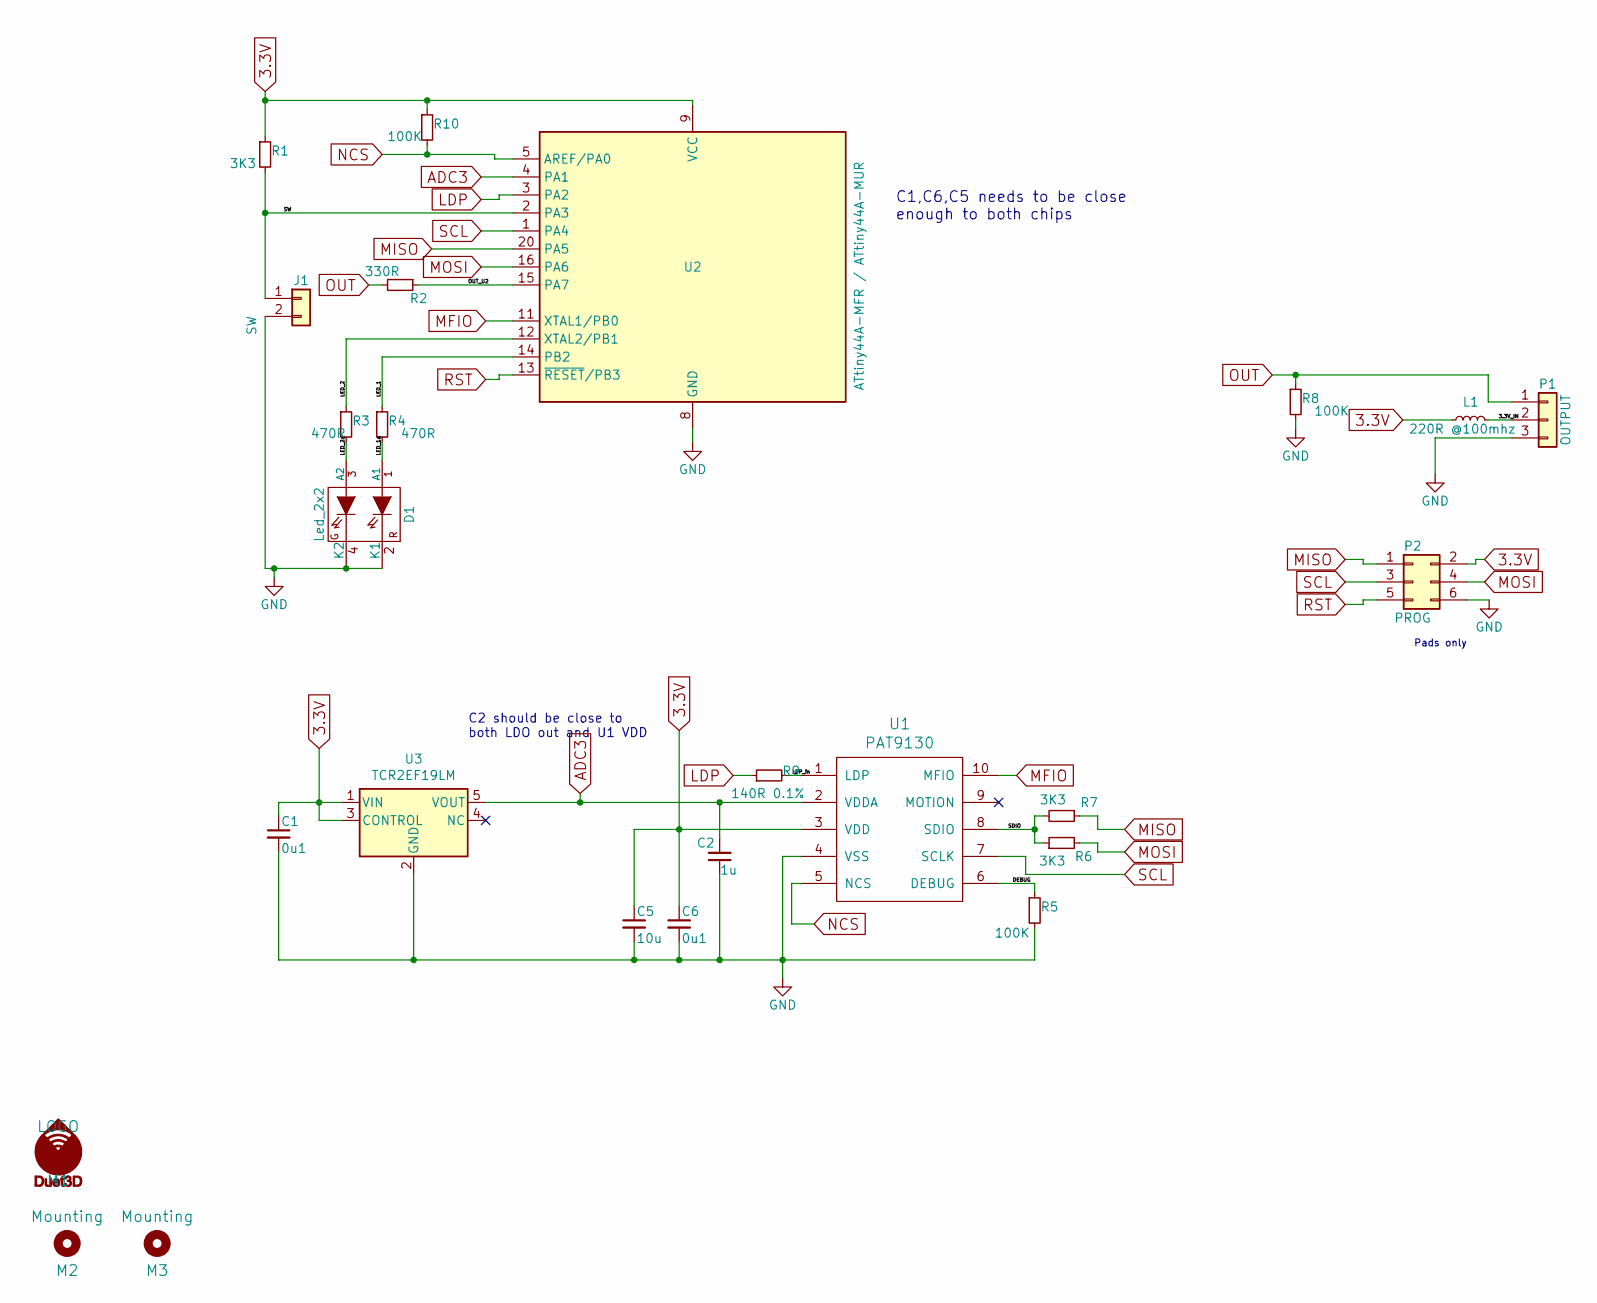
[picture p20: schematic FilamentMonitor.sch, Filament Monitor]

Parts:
C1, C6: 0u1; C_0603
C2: 1u; C_0805
C5: 10u; C_0805
D1: Led_2x2; 2x2_SMD_LED_1.6x1.25mm
J1: SW; PIN_ARRAY_2X1
L1: 220R @100mhz; R_0603
M1: LOGO; LOGO_Duet3dCompatible
M2, M3: Mounting; MountingHole_2.9mm
P1: OUTPUT; PIN_ARRAY_3X1
P2: PROG; Test_Point_2x3
R1, R6, R7: 3K3; R_0603
R2: 330R; R_0603
R3, R4: 470R; R_0603
R5, R8, R10: 100K; R_0603
R9: 140R 0.1%; R_0603
U1: PAT9130
U2: ATtiny44A-MFR / ATtiny44A-MUR; QFN-20-1EP_4x4mm_Pitch0.5mm
U3: TCR2EF19LM; SOT-23-5

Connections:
3.3V: C1.1, C5.1, C6.1, L1.1, P2.2, R1.1, R10.1, U1.3 (VDD), U2.9 (VCC), U3.1 (VIN), U3.3 (CONTROL)
/3.3V_IN: L1.2, P1.2
/DEBUG: R5.1, U1.6 (DEBUG)
/LDP_in: R9.2, U1.1 (LDP)
/LED_1: R4.1, U2.14 (PB2)
/LED_1a: D1.1 (A1), R4.2
/LED_2: R3.1, U2.12 (XTAL2/PB1)
/LED_2a: D1.3 (A2), R3.2
/OUT_U2: R2.1, U2.15 (PA7)
/SDIO: R6.1, R7.2, U1.8 (SDIO)
/SW: J1.1, R1.2, U2.2 (PA3)
ADC3: C2.2, U1.2 (VDDA), U2.4 (PA1), U3.5 (VOUT)
GND: C1.2, C2.1, C5.2, C6.2, D1.2 (K1), D1.4 (K2), J1.2, P1.3, P2.6, R5.2, R8.2, U1.4 (VSS), U2.8 (GND), U2.21 (GND), U3.2 (GND)
LDP: R9.1, U2.3 (PA2)
MFIO: U1.10 (MFIO), U2.11 (XTAL1/PB0)
MISO: P2.1, R7.1, U2.20 (PA5)
MOSI: P2.4, R6.2, U2.16 (PA6)
NCS: R10.2, U1.5 (NCS), U2.5 (AREF/PA0)
OUT: P1.1, R2.2, R8.1
RST: P2.5, U2.13 (~RESET~/PB3)
SCL: P2.3, U1.7 (SCLK), U2.1 (PA4)

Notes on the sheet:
Pads only
C1,C6,C5 needs to be close enough to both chips
C2 should be close to both LDO out and U1 VDD

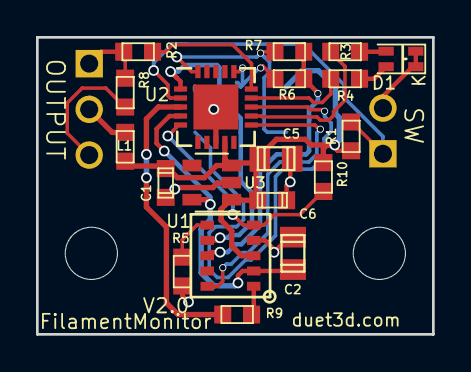
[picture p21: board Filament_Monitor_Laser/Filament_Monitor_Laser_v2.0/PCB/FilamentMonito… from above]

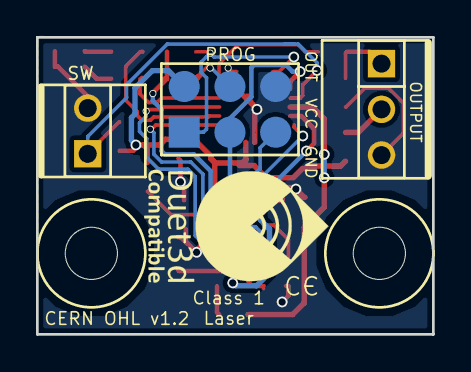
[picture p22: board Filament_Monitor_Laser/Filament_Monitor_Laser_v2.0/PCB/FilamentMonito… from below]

Board: 2 copper layers, 22.0 x 16.5 mm, 25 parts (6 on the bottom side), 21 nets.

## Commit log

2018-11-01 Laser Filament Monitor KiCAD Project
    See https://duet3d.dozuki.com/Wiki/Duet3dFilamentMonitor_LaserVersion
    [FilamentMonitor.kicad_pcb, FilamentMonitor.sch, FilamentMonitor.step]
2019-04-26 Added new housing
    for LFM v2.0
    [LaserFilamentSensorHousing_DC42_new.scad, LaserFilamentSensorHousing_DC42_new_base.stl, LaserFilamentSensorHousing_DC42_new_lid.stl]
2019-10-04 Added Magnetic Filament Monitor
    KiCad Source
    [FilamentMonitor.kicad_pcb, FilamentMonitor.sch]
2019-10-04 Magnet Filament Monitor enclosure
    [MFM_enc_body.stl, MFM_enc_idler.stl, MFM_enc_lid..stl]
2020-04-21 Added enclosure step files
    [MFM_enc_body.step, MFM_enc_idler.step, MFM_enc_lid.step]
2020-04-22 Added the IC3D 2.85mm housing
    [Body.stl, lid.stl]
2021-03-21 Added V2.0 KiCAD source
    [FilamentMonitor.kicad_pcb, FilamentMonitor.sch]
2021-09-01 Directory reorganisation
    [Body.stl, FilamentMonitor.kicad_pcb, FilamentMonitor.sch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]
2021-09-01 Added 1.7a info
    [FilamentMonitor.kicad_pcb, FilamentMonitor.sch, FilamentMonitor_v1.7a.step]
2021-09-27 Added enclosure v2 STLs
    [MFM_Body_v2.stl, MFM_Idler_v2_print2.stl, MFM_Lid_v2.stl]
2021-09-27 M3 clearance version of the enclosure body
    [MFM_Body_v2_m3_clearance_for_mounting.stl]
2021-11-13 added a zip file of the three stls
    [MFM_enc_lid.stl]
2021-11-13 Updated readme and added zip for enclosure v2
2022-12-02 Added the version 3 enclosure
    [MFM_Idler_v3_x2.stl, MFM_enclosurev3_body_seam_0.2layer1.stl, MFM_enclosurev3_lid_seam_0.2layer1.stl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]
2022-12-02 added the body version with m3 clearance mounting holes.
    [MFM_enclosurev3_body_seam_0.2layer1_m3_clearance.stl]
2023-02-03 v1.7b added
    [FilamentMonitor.step]
2025-02-22 add assembled STEP
    [FILAMENT-MONITOR-v3.STEP]

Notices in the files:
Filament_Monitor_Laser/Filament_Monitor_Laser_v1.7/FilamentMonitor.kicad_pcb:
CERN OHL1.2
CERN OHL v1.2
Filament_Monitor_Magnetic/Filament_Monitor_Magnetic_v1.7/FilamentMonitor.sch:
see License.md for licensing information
